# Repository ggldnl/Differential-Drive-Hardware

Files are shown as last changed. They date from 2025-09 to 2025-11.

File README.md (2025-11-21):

# Differential Drive – Hardware

This repository contains the Gerber files, Bill of Materials and STL/3MF files for my Differential Drive robot.

Take also a look to the [repository containing the Controller](https://github.com/ggldnl/Differential-Drive-Controller.git).
I documented the design process, construction and theory in [this article](https://ggldnl.github.io/projects/differential_drive/index.html).

## PCB and Electronics

<div style="display: flex; justify-content: center; gap: 10px;">
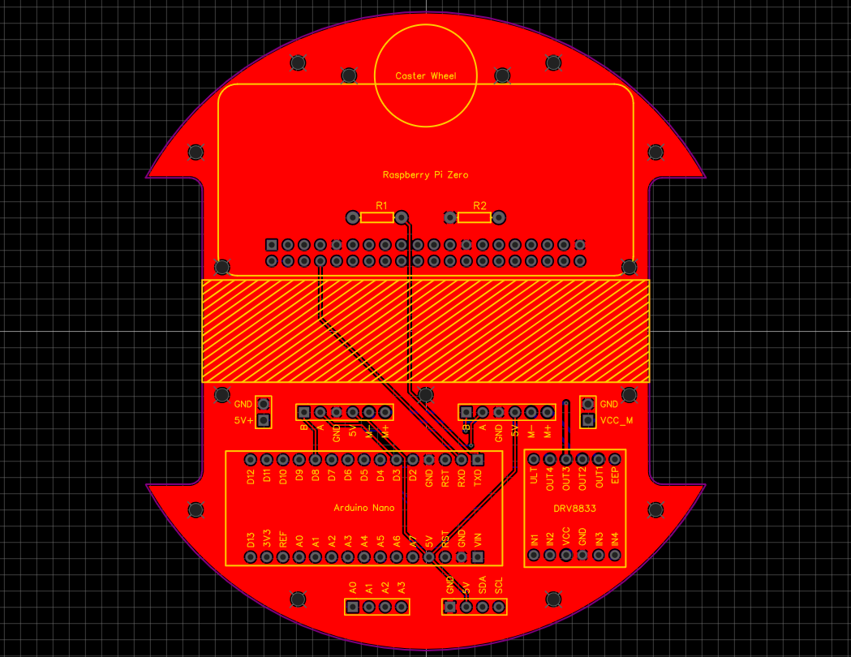
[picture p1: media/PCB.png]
  
  PCB Render
</div>
</br>

Summary of the main components and their function:

| Component | Description |
| --- | --- |
| Raspberry Pi Pico | Main processing unit. Can act as a high-level node in a larger system, receiving messages from external processes and sending commands to the Arduino.|
| Arduino Nano | Near-real time processing unit managing motor control, sensors, communication, ... |
| DRV8833 Dual H-Bridge | Controls the direction and speed of two DC motors using PWM signals. |
| N20 Geared DC Motors (60RPM) | Provide locomotion for the differential drive; each of them has a magnetic encoder. |
| I2C Interfacing connector | Connector to interface with I2C devices. |
| Analog A0-A3 pins connector | Reserved for future expansion; provides access to pins A0-A3; can be used to read analog sensors or control inputs. |

## Mechanical Design

<div>
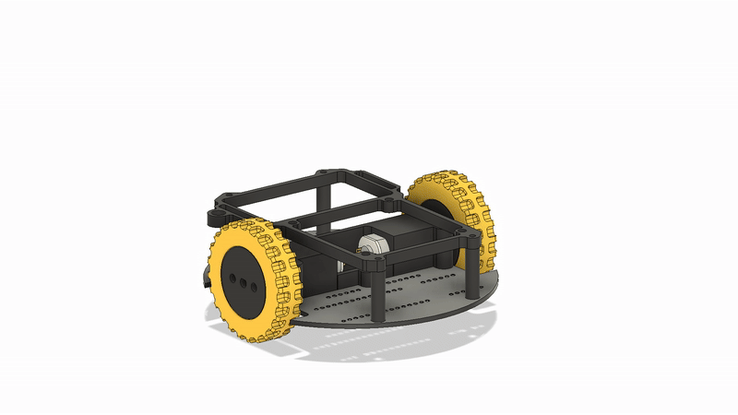
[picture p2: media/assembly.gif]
  
</div>
</br>

The mechanical assembly consists of 3D-printed structural parts and a small set of standard hardware components. The PCB is directly used as chassis to provide a rigid base where to mount the 3d printed parts.

All the parts are printed in PLA except for the tires that are printed in TPU.

## Complete BIll of Materials

| Component | Quantity | Notes |
|---|---|---|
| Raspberry pi pico | 1 | |
| Arduino Nano | 1 | |
| DRV8833 | 1 | |
| N20 Geared DC Motor (60RPM) | 2 | You can find multiple versions of these motors that looks very similar to each other; the only things that changes is the gear ratio and thus the max RPM |
| Battery | 1 | I used a 2S 500mAh Lipo battery; similar ones are commonly found in RC planes and cars. You can use different batteries, the regulator should support 2-6S Lipo (7-25.5V). |
| ZMR 8A Dual BEC | 1 | Difficult to find documentation about it, you can use something else. |
| 2x20 Female headers | 1 | To mount the Raspberry |
| 1x15 Female headers | 2 | To mount the Arduino | 
| 1x6 Female headers  | 2 | To mount the DRV8833 |
| 1x4 JST-XH Female connector | 2 | For the two expansion set of pins |
| Metal ball with a 10mm diameter | 1 | Caster wheel |
| M2 Heat set inserts | 21 | |
| M2 6mm screw | 21 | |
| On/off Switch | 1 | The 3d printed mount is compatible with a DPDT Mini Toggle Switch | 

## 🤝 Contribution
Feel free to contribute by opening issues or submitting pull requests. For further information, check out the [repository containing the Controller](https://github.com/ggldnl/Differential-Drive). Give a ⭐️ to this project if you liked the content.

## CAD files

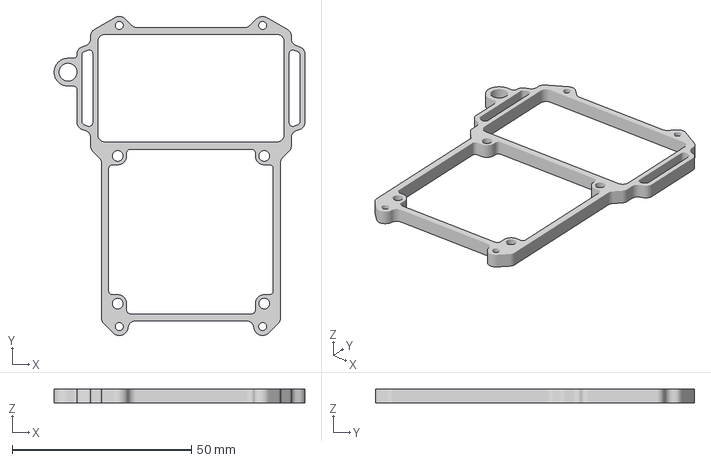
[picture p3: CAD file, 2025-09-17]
printed_parts/3mf/power_supply_battery_mount_with_switch.3mf
70.0 x 89.0 x 4.00 mm

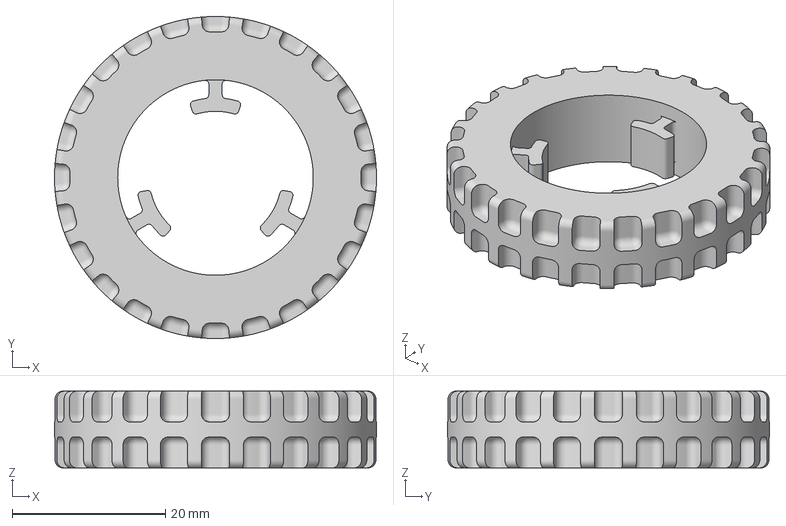
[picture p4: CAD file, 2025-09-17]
printed_parts/3mf/wheel_tire.3mf
42.0 x 42.0 x 10.0 mm

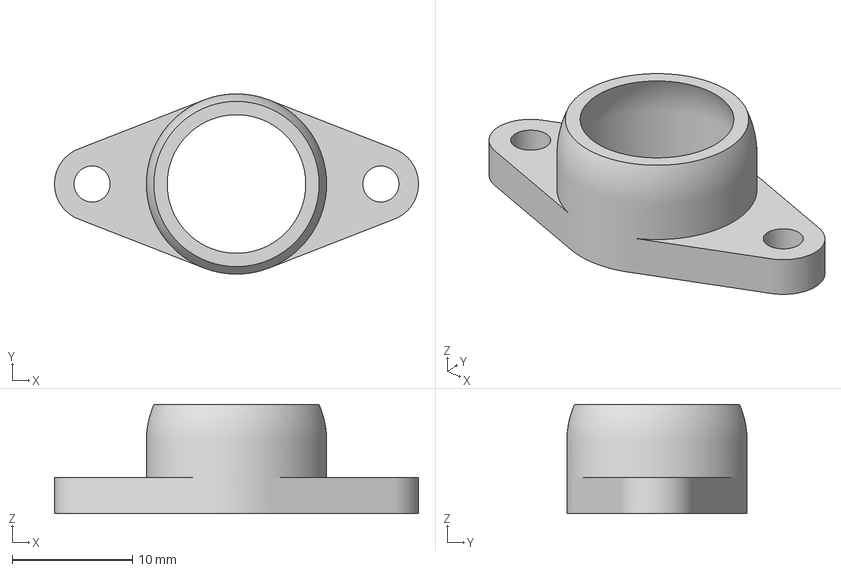
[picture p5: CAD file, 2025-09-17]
printed_parts/3mf/ball_caster_mount.3mf
30.2 x 15.0 x 9.06 mm

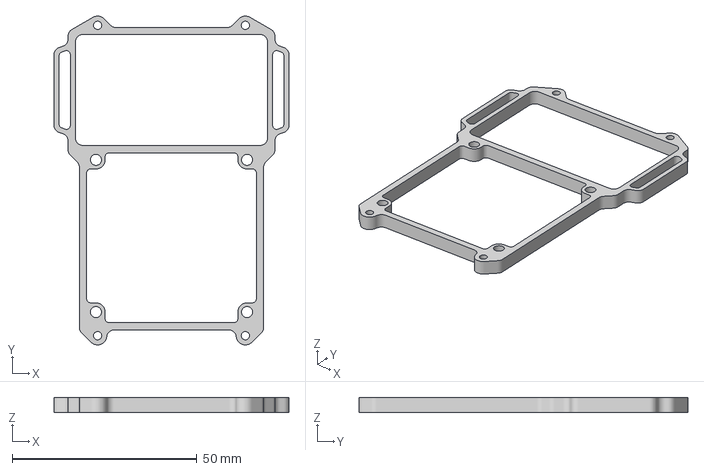
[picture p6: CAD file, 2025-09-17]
printed_parts/3mf/power_supply_battery_mount.3mf
63.6 x 89.0 x 4.00 mm

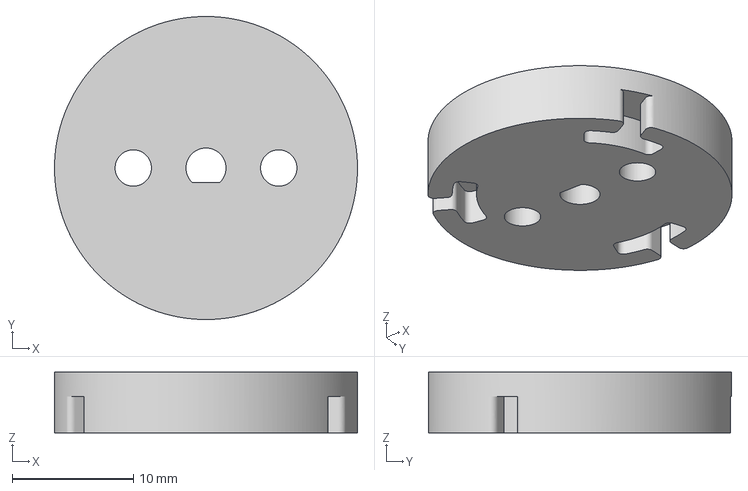
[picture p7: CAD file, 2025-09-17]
printed_parts/3mf/wheel_hub_top.3mf
25.0 x 25.0 x 5.00 mm

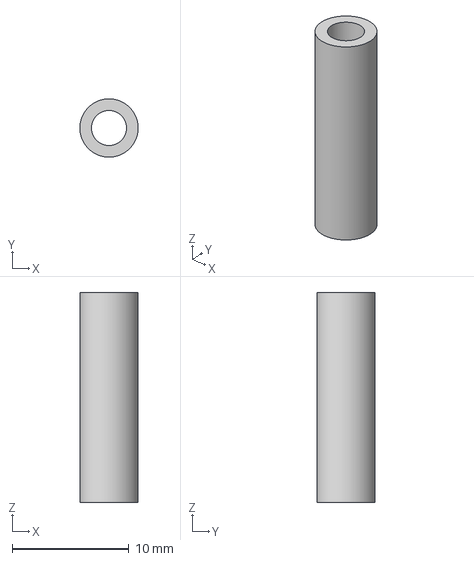
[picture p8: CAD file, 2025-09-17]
printed_parts/3mf/spacer.3mf
5.00 x 5.00 x 18.0 mm

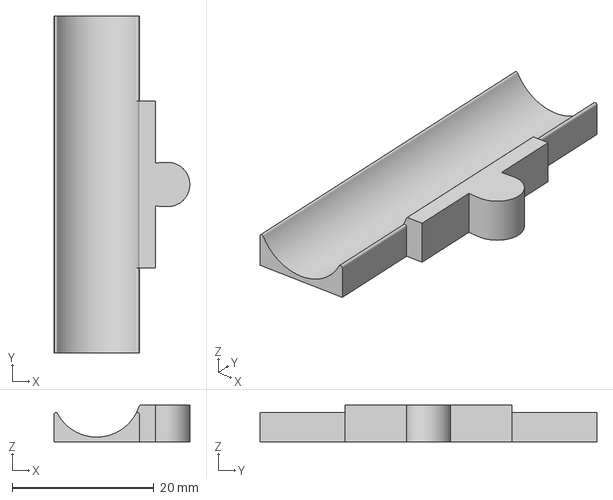
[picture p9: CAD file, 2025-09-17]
printed_parts/3mf/motor_mount_bottom.3mf
19.1 x 47.5 x 5.17 mm

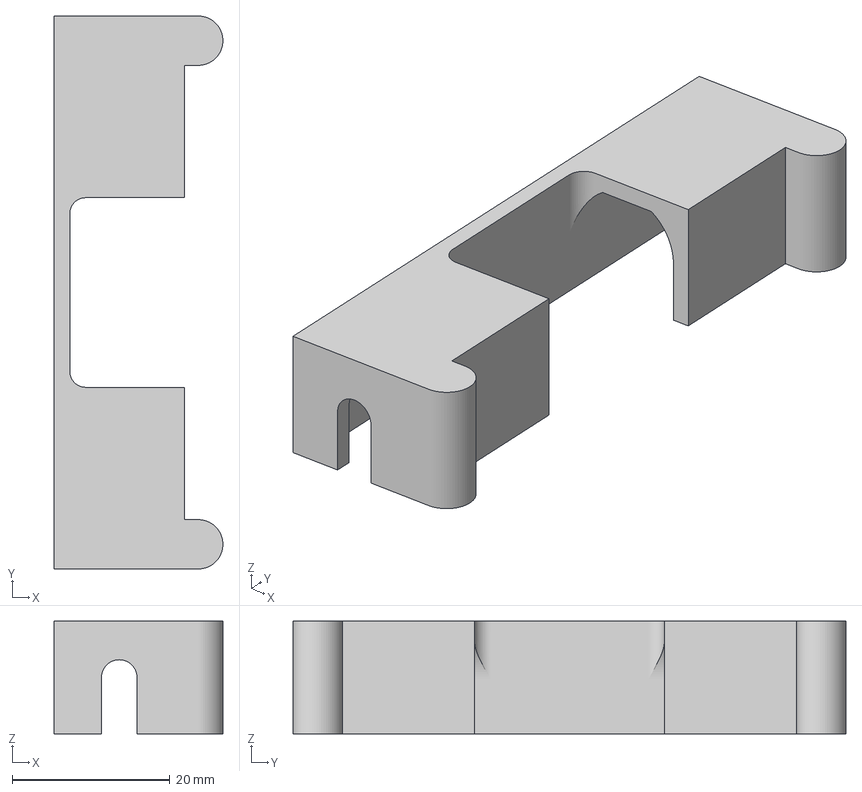
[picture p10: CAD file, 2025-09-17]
printed_parts/3mf/motor_mount_top.3mf
21.4 x 70.0 x 14.2 mm

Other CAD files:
printed_parts/3mf/wheel_hub_bottom.3mf
printed_parts/stl/ball_caster_mount.stl
printed_parts/stl/motor_mount_bottom.stl
printed_parts/stl/motor_mount_top.stl
printed_parts/stl/power_supply_battery_mount.stl
printed_parts/stl/power_supply_battery_mount_with_switch.stl
printed_parts/stl/spacer.stl
printed_parts/stl/wheel_hub_bottom.stl
printed_parts/stl/wheel_hub_top.stl
printed_parts/stl/wheel_tire.stl
